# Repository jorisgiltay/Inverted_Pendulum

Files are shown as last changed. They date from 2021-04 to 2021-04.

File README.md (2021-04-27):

# Inverted Pendulum
Repo for different files regarding inverted pendulum project.

Eventual goal of this project is to train a Convolutional Neural Network (CNN), on simulated pendulum footage.

Then let the pendulum be stabilized by the CNN, as a proof that the setup is controllable and can work mechanically, I implemented LQR control first. 

Used quite some code from [this project](https://create.arduino.cc/projecthub/zjor/inverted-pendulum-on-a-cart-199d6f) , which was a huge help! 

Pictures of the first prototype below:

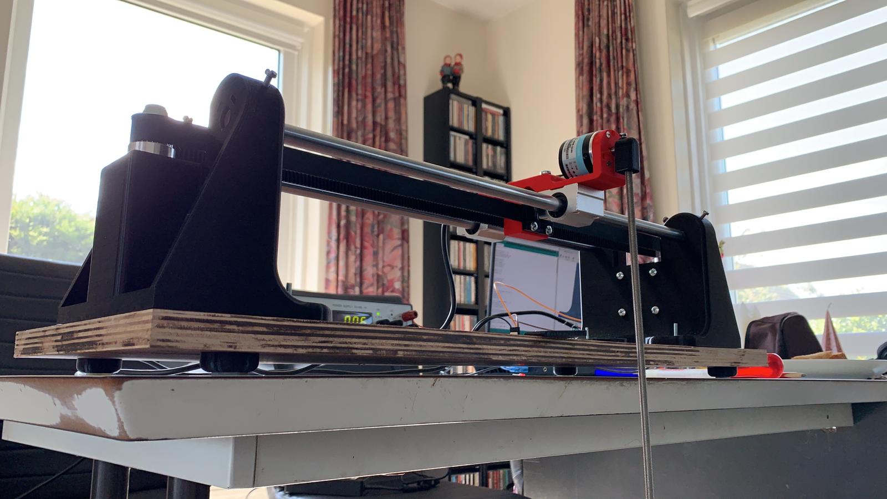
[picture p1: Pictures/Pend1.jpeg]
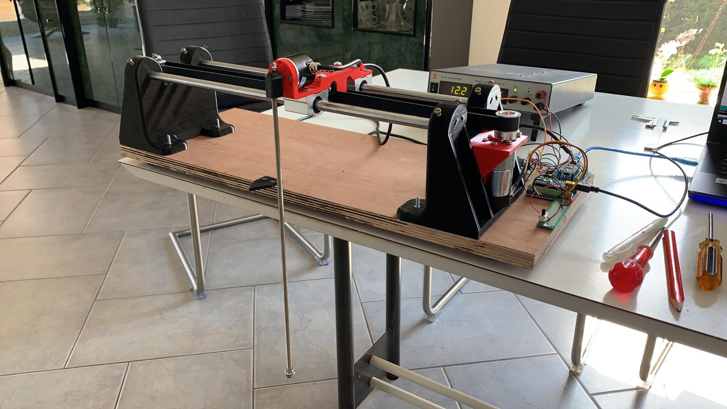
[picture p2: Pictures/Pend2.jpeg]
, 

And a picture of it doing its job :)

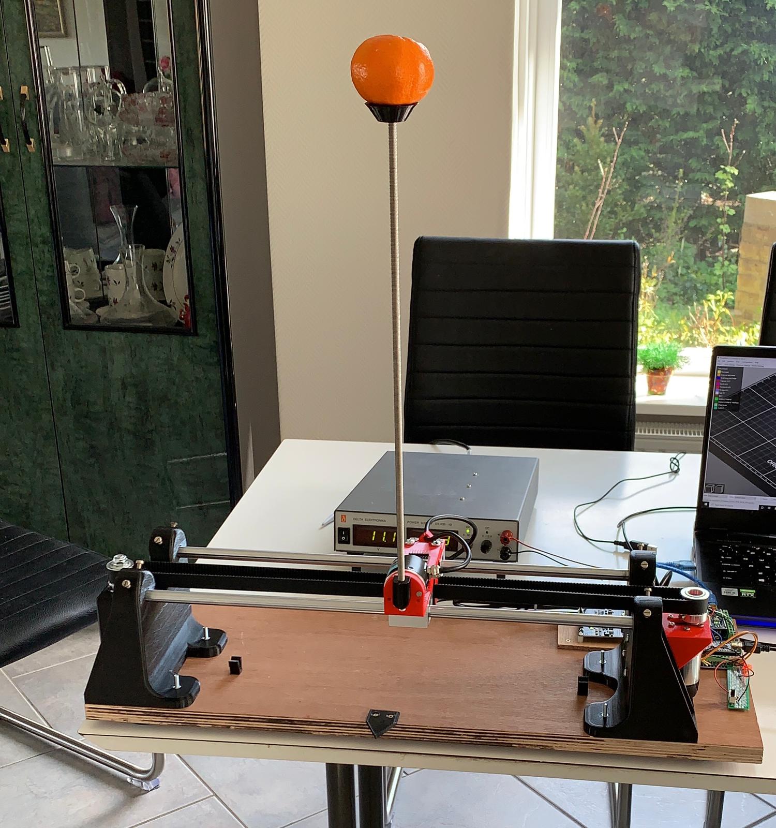
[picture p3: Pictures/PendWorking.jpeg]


# Hardware (LQR control)

## Components:

* 2x Arduino Nano
* 1x Cytron 10Amp 5-30 V DC Motor Driver
* 1x Variable Power Supply
* 1x 600P / R-encoder
* 1x 12v 251 RPM DC Motor (43.8:1) (with encoder)
* 2x 500mm, 12mm diameter steel rods
* 2x SC12UU slider bearings
* 1x HTD 3M pulley (24 teeth, bore diameter 8)
* 1x HTD 3M pully (24 teeth, bore diameter 14)
* 1x 1000mm HTD 3M timing belt
* 1x 150mm M8 threaded rod
* 1x 400mm M6 threaded rod
* Some 3d printed parts(STL's included)
* MPU6050 (optional, not currently used)
* 20 mA LED, 270 Ohm resistor, switch button
* Bunch of M3, M4 and M5 nuts and bolts
* Wooden plank of 600mm by 250mm

## Animation of the CAD model:

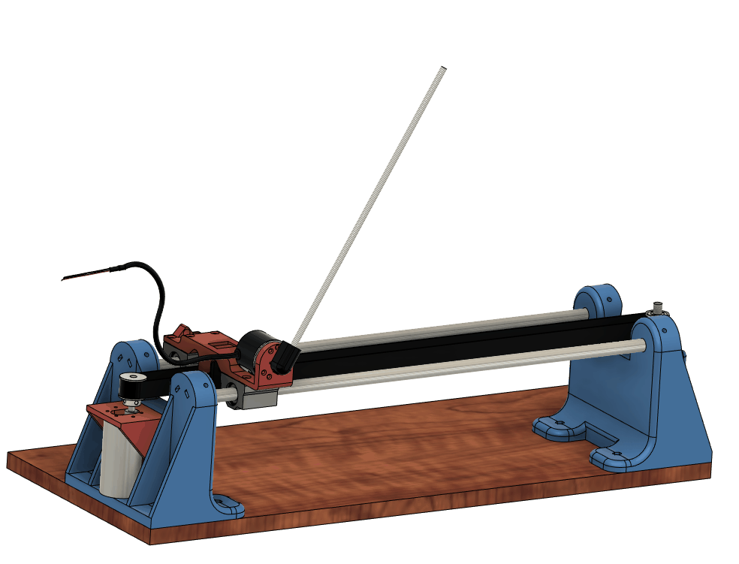
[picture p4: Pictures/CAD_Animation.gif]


# Software
The pendulum will try and swing up between hard set bounds (140mm on each side). When it enters a controllable region the LQR control takes over (click on link for video):

Demo (https://www.youtube.com/watch?v=xbCsyzsChe0)

The 2 arduino nano's communicate over ISP, the main reason for using another Arduino is that we do not suffer resolution loss of the encoder of the motor and pendulum, because we can use both the A and B channels of the quadrature signal on interuptable pins (pins 2 and 3)

# TODO

- [x] Add feet with silicon strip to prevent sliding 
- [x] Add middle of rails indicator 
- [ ] Rearrange wiring
- [ ] Get small 12V (~200Watt) power supply
- [ ] Read out cart accelerations with MPU6050
- [ ] Migrate to NVIDIA Jetson Nano 
- [ ] Add double pendulum (need to find a way to neatly fix wiring for third encoder for this)
- [ ] Make the thing sort of portable

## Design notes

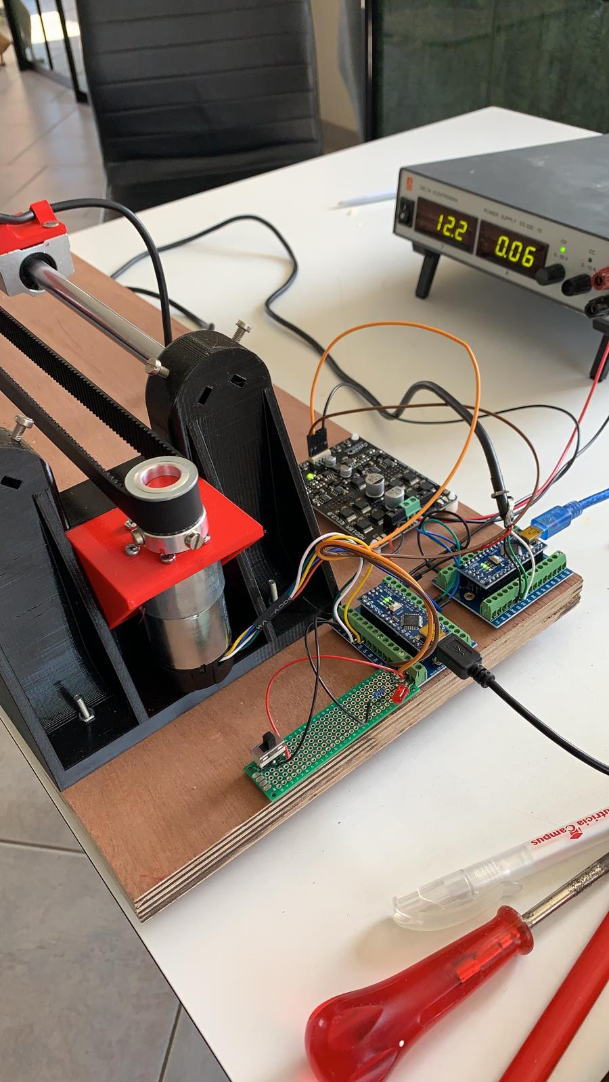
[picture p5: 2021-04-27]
Pictures/Pend3.jpeg

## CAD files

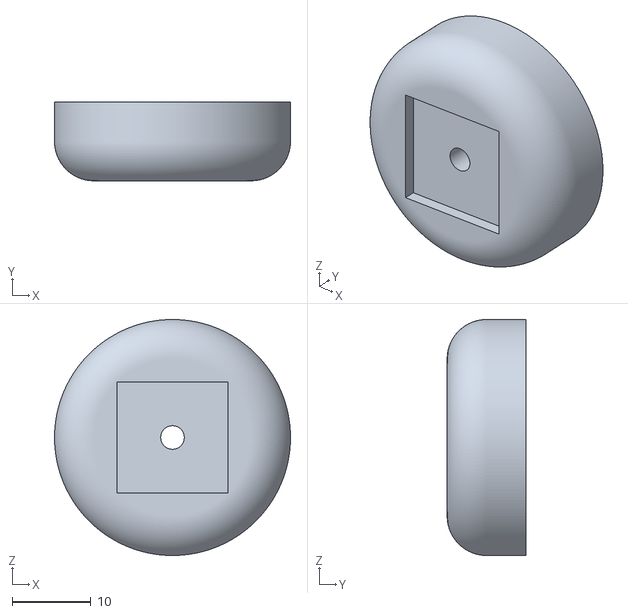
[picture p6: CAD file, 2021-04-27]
STL_Files/Feet.stl
30.0 x 10.0 x 30.0

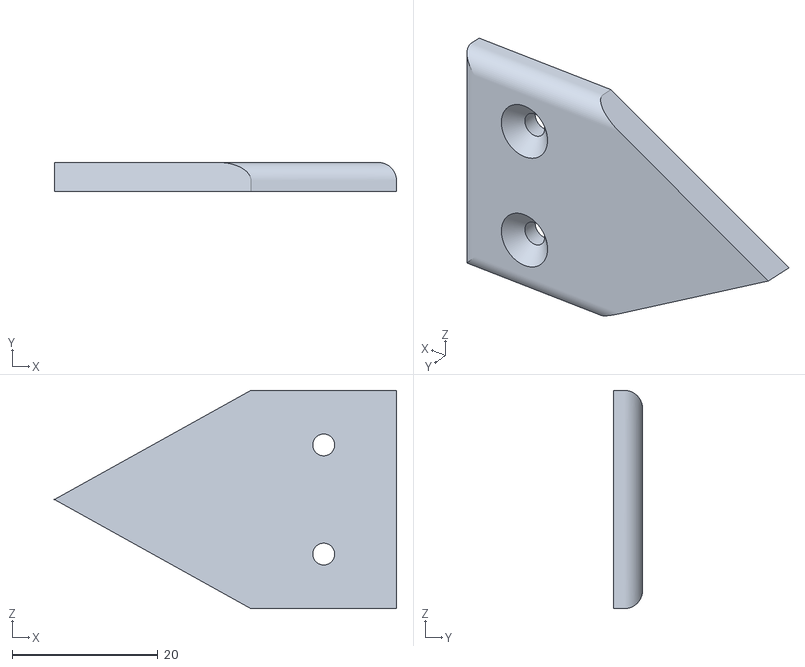
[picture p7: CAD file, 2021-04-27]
STL_Files/MiddleIndicator.stl
47.0 x 4.00 x 30.0

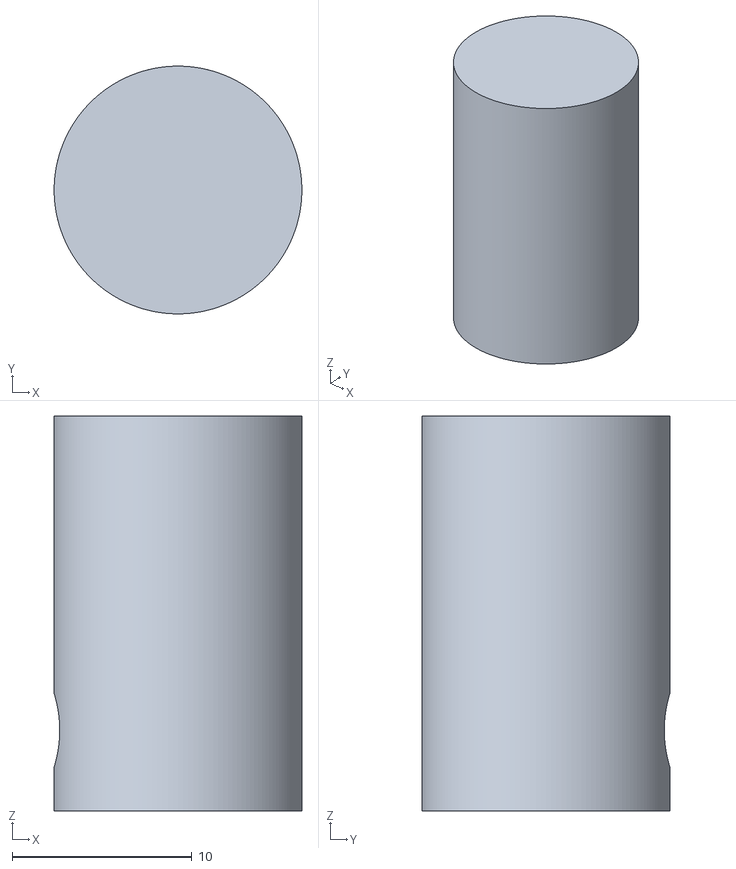
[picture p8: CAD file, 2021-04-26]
STL_Files/ShaftAdapter.stl
13.8 x 13.8 x 22.0

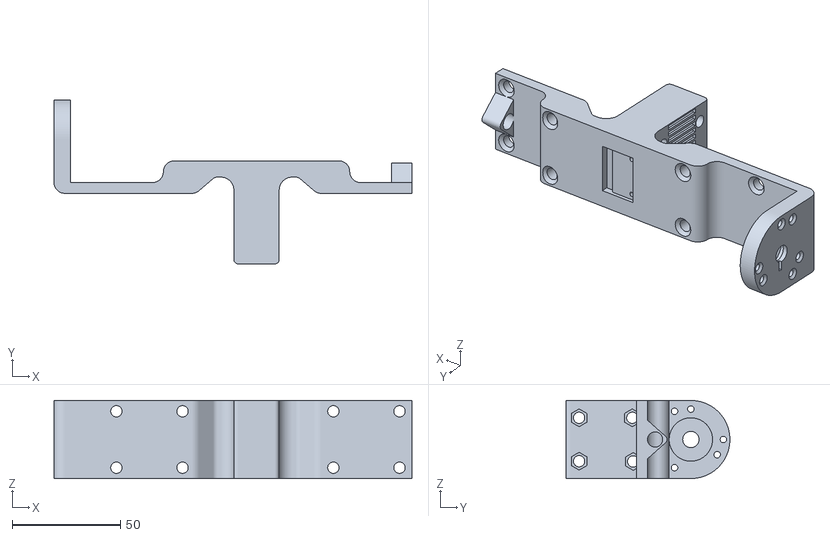
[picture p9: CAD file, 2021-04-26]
STL_Files/Carriage.stl
165.0 x 75.5 x 36.0

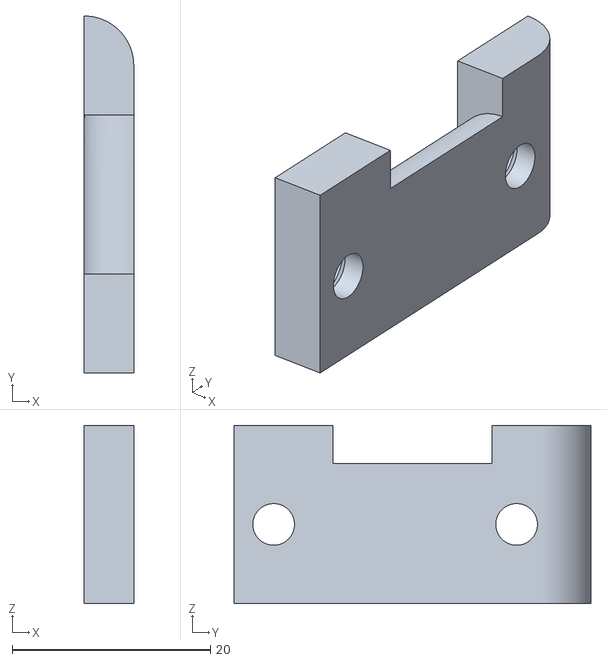
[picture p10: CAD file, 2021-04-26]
STL_Files/ClampholderRight.stl
5.00 x 36.0 x 18.0

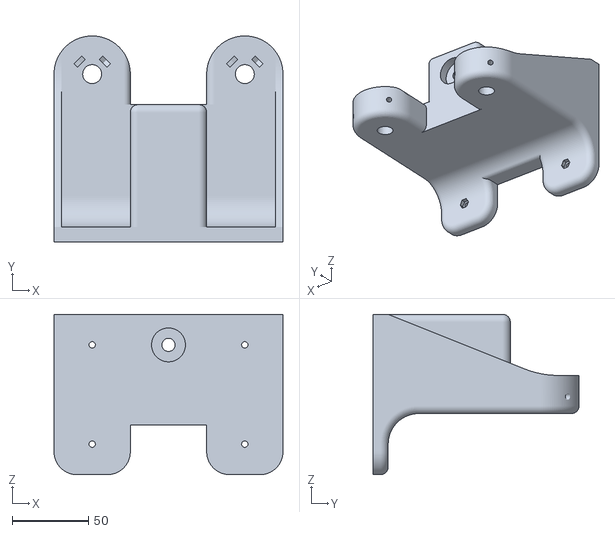
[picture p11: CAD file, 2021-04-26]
STL_Files/RodHolderLeft.stl
150.0 x 135.0 x 105.0

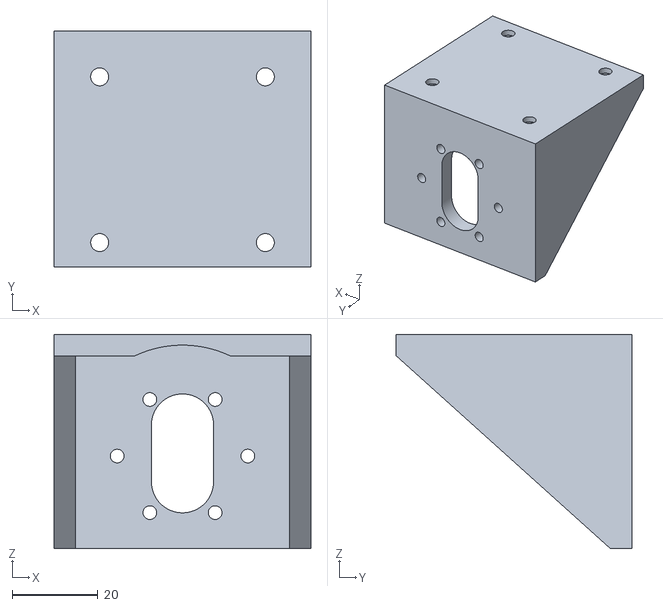
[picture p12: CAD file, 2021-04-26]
STL_Files/DCMotorMount.stl
60.0 x 55.0 x 50.0

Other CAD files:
STL_Files/ClampholderLeft.stl
STL_Files/RodHolderRight.stl

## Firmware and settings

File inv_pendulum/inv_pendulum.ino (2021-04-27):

#include <Wire.h>

#define REF_OUT_A 2 // PD3
#define REF_OUT_B 3 // PD2
#define MOTOR_ENCODER_PPR  2797
#define POSITION_LIMIT 0.18

#define PWM_PIN 10
#define DIR_PIN 8
#define SHAFT_R 0.011
#define BTN_PIN 11
#define LED_PIN 12

#define A 18.08
#define B 0.37
#define C 0.15


// 40cm (works okay)
#define Kx  3.05
#define Kv  3.4
#define Kth 22.5
#define Kw  4.4


//// 40cm trials works a bit faster on x
//#define Kx  9.6
//#define Kv  7.5
//#define Kth 32.5
//#define Kw  6.7

const float THETA_THRESHOLD = PI / 16;
bool moveleft = true;
bool from_control = false;
bool return_to_center = false;

volatile long refEncoderValue = 0; // for encoder motor
volatile long lastRefEncoded = 0;

volatile float theta;   //for i2c comm
volatile float theta_dot;

unsigned long now = 0L;
unsigned long lastTimeMicros = 0L;

float x, v, dt, elapsed, RPM;
float last_x, last_v;
float control, u;
const float PI2 = 2.0 * PI;
int PWM;


void refEncoderHandler();

void setup() {
  delay(3000);
  Wire.begin(4);                // join i2c bus with address #4
  Wire.onReceive(receiveEvent); // register event
  // put your setup code here, to run once:

  TCCR2B = TCCR2B & B11111000 | B00000001;
  
  pinMode(REF_OUT_A, INPUT_PULLUP);
  pinMode(REF_OUT_B, INPUT_PULLUP);

  pinMode(BTN_PIN, INPUT_PULLUP);
  pinMode(LED_PIN, OUTPUT);

  pinMode(PWM_PIN, OUTPUT);
  pinMode(DIR_PIN, OUTPUT);

  
  
  attachInterrupt(digitalPinToInterrupt(REF_OUT_A), refEncoderHandler, CHANGE);
  attachInterrupt(digitalPinToInterrupt(REF_OUT_B), refEncoderHandler, CHANGE);

  Serial.begin(57600);
  
  PWM = 0;
  analogWrite(PWM_PIN, PWM);
  lastTimeMicros = 0L;

}

void loop() {
  //Only loop this when the switch is turned on, if not return to center.
  if(digitalRead(BTN_PIN) == 0){
      x = getCartDistance(refEncoderValue, MOTOR_ENCODER_PPR);
      while(x > 0.001){
        x = getCartDistance(refEncoderValue, MOTOR_ENCODER_PPR);
        driveMotor(-70);
          }
      while(x < -0.001){
        x = getCartDistance(refEncoderValue, MOTOR_ENCODER_PPR);
        driveMotor(70);
      }
        driveMotor(0);
     
    
    digitalWrite(LED_PIN, LOW);
  }
  else{
    digitalWrite(LED_PIN, HIGH);
    now = micros();
    dt = 1.0 * (now - lastTimeMicros) / 1000000;
    elapsed += dt;
  
    // Get States (note that the other states Theta and thetadot are received via I2C (receiveEvent))
    x = getCartDistance(refEncoderValue, MOTOR_ENCODER_PPR);
    v = (x - last_x) / dt;
    if (abs(x - last_x) > 100){
      v = last_v;
    }
  
    if (isControllable(theta) && fabs(x) < POSITION_LIMIT && return_to_center == false) {
      from_control = true;
      control = (Kx * x + Kv * v + Kth * theta + Kw * theta_dot);
      u = (control + A * v + copysignf(C, v)) / B;
      u = 255.0 * u / 12.0;
      driveMotor(saturate(u, 220));
    } else {
      driveMotor(0);
    }
  
    // Swing back up if LQR failed
    if (!isControllable(theta) && fabs(x) < POSITION_LIMIT && from_control == false && return_to_center == false){
  
      if(fabs(theta) > 2  && theta_dot >= 0){
          driveMotor(220);
      }
      else if (fabs(theta)> 2 && theta_dot <0){
          driveMotor(-220);
      }
    }
  
    // Return to center when reaching the endpoints
    if (return_to_center == true){
      while(x > 0.001){
        x = getCartDistance(refEncoderValue, MOTOR_ENCODER_PPR);
        driveMotor(-70);
        }
      while(x < -0.001){
        x = getCartDistance(refEncoderValue, MOTOR_ENCODER_PPR);
        driveMotor(70);
      }
        driveMotor(0);
        return_to_center = false;
  
     }
      
    // Boolean logic for the different scenarios
    if (fabs(x) >= POSITION_LIMIT){
      return_to_center = true;
    }
  
    if(fabs(theta_dot) <5 && fabs(theta) > 1){
      from_control = false;
    }
  
    last_x = x;
    last_v = v;
    lastTimeMicros = now;
  
     
    Serial.println(theta);
    Serial.print(",");
    Serial.print(theta_dot);
    Serial.print(",");
    Serial.print(x);
    Serial.print(",");
    Serial.println(v);
    delay(5);
  }
}

boolean isControllable(float theta) {
  return fabs(theta) < THETA_THRESHOLD;
}

float getCartDistance(long pulses, long ppr) {
  return 2.0 * PI * pulses / MOTOR_ENCODER_PPR * SHAFT_R;
}

float getAngle(long pulses, long ppr) {  
  float angle = (PI + PI2 * pulses / ppr);
  while (angle > PI) {
    angle -= PI2;
  }
  while (angle < -PI) {
    angle += PI2;
  }
  return angle;
}

float saturate(float v, float maxValue) {
  if (fabs(v) > maxValue) {
    return (v > 0) ? maxValue : -maxValue;
  } else {
    return v;
  }
}

void driveMotor(float u) {
  digitalWrite(DIR_PIN, u > 0.0 ? LOW : HIGH);
  analogWrite(PWM_PIN, fabs(u));
}

void refEncoderHandler() {
  int MSB = (PIND & (1 << PD2)) >> PD2; //MSB = most significant bit
  int LSB = (PIND & (1 << PD3)) >> PD3; //LSB = least significant bit
  int encoded = (MSB << 1) | LSB; //converting the 2 pin value to single number
  int sum  = (lastRefEncoded << 2) | encoded; //adding it to the previous encoded value

  if(sum == 0b1101 || sum == 0b0100 || sum == 0b0010 || sum == 0b1011) {
    refEncoderValue++; //CW
  }
  if(sum == 0b1110 || sum == 0b0111 || sum == 0b0001 || sum == 0b1000) {
    refEncoderValue--; //CCW
  }

  lastRefEncoded = encoded; //store this value for next time  
}

void receiveEvent(int howMany)
{
  //Serial.println(howMany);
  uint8_t total_bytes[8] = {0, 0, 0, 0, 0, 0, 0, 0}; // fill this array with the four bytes you received
  uint8_t theta_bytes[4] = {0,0,0,0};
  uint8_t theta_dot_bytes[4] = {0,0,0,0};
  for (int i = 0; i<8; i++){
    total_bytes[i] = Wire.read();
  }
  for (int k = 0; k <4; k++){
  theta_bytes[k] = total_bytes[k];
  theta_dot_bytes[k] = total_bytes[k+4];
  }
  
    memcpy(&theta, &theta_bytes, sizeof(theta));
    memcpy(&theta_dot, &theta_dot_bytes, sizeof(theta_dot));
}

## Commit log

2021-04-23 added testing sketches for encoders
2021-04-23 added backup CAD files
2021-04-25 added matlab motor parameter estimation
    [experiment_giltay.csv]
2021-04-26 Added CAD Animation
2021-04-26 added STLs
    [Carriage.stl, ClampholderLeft.stl, ClampholderRight.stl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]
2021-04-26 added shaft adapter
    [ShaftAdapter.stl]
2021-04-26 added DC version CAD f3d file
2021-04-27 added last STLs
    [Feet.stl, MiddleIndicator.stl]
2021-04-27 added first prototype pictures
